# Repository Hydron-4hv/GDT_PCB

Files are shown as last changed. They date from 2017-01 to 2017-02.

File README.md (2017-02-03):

# GDT_PCB
PCB for drive circuitry and Gate Drive Transfomer, for driving IGBT half-bridge PCBAs in Tesla Coil application

# WARNING:
The creepage/clearance distances on this PCB between the bridge voltages (i.e. those present of the output of the GDT) and the low voltage circuitry is not large (1mm), and thus nothing connected to this PCB (including the driver controller connected via the RJ45 connectors) should be touched while mains voltage is applied. Unless an isolation tranformer is used to supply the bridge DC bus voltage, everything except mains protective earth should be treated as live.

Notes:
- To be used with the PCB from the either the "IGBT_half_bridge" or "QCW_half_bridge_PCB" repos, 2 off for full bridge setup, 4 for dual full-bridge.
- A hand wound gate drive transformer is required.
  - I am planning to wind one with RG-174 co-ax (for high coupling), with primary side being the shield, secondary being the centre conductor.
  - A full bridge setup needs 2 windings on each core, and won't use all four winding connections or output connectors.
  - Will supply pictures once I have built the PCB and wound the transformers
- To drive extra half bridges a second PCB can be "slaved" to the first using the expansion connection. An output variant has been created named "SLAVE" to show this
- PDF schematics, 3D info, BoMs etc are located within the "Reference Outputs" directory
- Note that the regulator for the "12V" net is actually a 5V output part - anything in the range of 5V-12V should work OK.
- The 24V input can be lowered if the desired gate drive voltage to the IGBTs is less than this.
- The 3x 1000uF 25V capacitors are unnecessarily large for low pulse length applications (e.g. standard non-QCW DRSSTC). These should be replaced by smaller, 35V rated parts if the board is not used in a CW or QCW application.

Note: changes planned for next revision:
- Improve creepage distance as possible. Isolation slots.
- Potential to add transformer isolation for CT input from ribbon cables
- Use RS485 for gate drive signal input from RJ45 for increased noise immunity. (High priority)
- Add power status LED
- "12V" to be renamed to "5V", and supply also used for RS485 receiver
- Use switchmode DC/DC on the PCB rather than in a module
- Capacitor voltage specifications in "Gate Driver" sub section to be increased to 35/50V from 25V. Parts are available in the same package with increased rating.
- Fix DC jack footprint (add locating hole)
- Potential addition of fan/temperature control/measurement
- Change TVS footprints for fitting lower capacitance parts (e.g. SOT-23)
- Fix major pinout problem for drive FETs (CAD software decided to flip component for no reason)

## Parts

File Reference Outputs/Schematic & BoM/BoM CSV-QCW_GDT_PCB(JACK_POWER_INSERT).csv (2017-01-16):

Designator | Comment | Description | Fitted | Footprint | LibRef | Quantity
A_1, A_2, B_1, B_2 | Testpoint |  | Fitted | Keystone5002 | Testpoint | 4
C1, C2, C3 | EEU-FM1E102 | CAP ALUM 1000UF 20% 25V RADIAL | Fitted | 12.5mm lytic | Electrolytic Capacitor | 3
C4, C5, C31_1, C31_2 | CC0805KKX7R7BB105 | CAP CER 1UF 16V X7R 0805 | Fitted | 0805C | Capacitor | 4
C6, C7 | 885012209028 |  | Fitted | 1210C | Capacitor | 2
C26_1, C26_2 | GRM31MR71H105KA88L | CAP CER 1UF 50V X7R 1206 | Fitted | 1206C | Capacitor | 2
C27_1, C27_2, C30_1, C30_2 | 885012209028 | CAP CER 10UF 25V X7R 1210 | Fitted | 1210C | Capacitor | 4
C28_1, C28_2 | CGA6M3X7R1H225K200AB | CAP ALUM 100UF 20% 16V RADIAL | Fitted | 1210C | Capacitor | 2
C29_1, C29_2, C32_1, C32_2 | 08055C104JAT2A | CAP CER 0.1UF 50V X7R 0805 | Fitted | 0805C | Capacitor | 4
C37_1, C37_2, C38_1, C38_2 | C0805C102K5RACTU | CAP CER 1000PF 50V X7R 0805 | Fitted | 0805C | Capacitor | 4
D1, D2 | 600 W, 24 VDC | WE-TVSP Power TVS Diode, bidirectional, 600 W, 24 VDC | Fitted | DO-214AA_Bidirectional | WE-TVSP DO-214AA, 824521241 | 2
D7_1, D7_2, D8_1, D8_2 | MCL4148-TR | DIODE GEN 75V 150MA MICROMELF | Fitted | MicroMELF | 1N4148 | 4
FB1, FB2, FB3, FB4 | FerriteBead | Ferrite Bead | Fitted | 0805FB | FerriteBead | 4
J1, J3, J5, J7 | 61202021621 | WR-BHD 2.54mm Male Box Header | Fitted | 61202021621 | 61202021621 | 4
J2, J4 | 61500814221 | WR-MJ Modular Jack Horizontal Shielded 8P8C Tab Down | Fitted | 61500814221 | 61500814221 | 2
J6 | BNC_1 | BNC Connector | Fitted | BNC_PLASTIC_ELBOW_SOCKET_WITH_MOUNTING_POSTS | BNC_1 | 1
J8, J13 | 22-23-2021 | Pin Header, 2 Position, Locking, .1 Centers | Fitted | 22-23-2021 | 22-23-2021 | 2
J9 | 61201621621 | WR-BHD 2.54mm Male Box Header | Fitted | 61201621621 | 61201621621 | 1
J10 | POWER_J | Low Voltage Power Supply Connector | Fitted | POWER_J_SLOT |  | 1
J11 | Header_3_right_angle_th_3.81mm | 3-way header | Fitted | 691322310003 | Header_3_right_angle_th_3.81mm | 1
J12 | Header_2_5.08mm_Screw_Black | 2-way PCB connector | Not Fitted | 1776119-2 | Header_2_5.08mm_Screw_Black | 0
Q3_1, Q3_2, Q4_1, Q4_2 | DMC3021LK4-13 | MOSFET N/P-CH 30V TO252-4L | Fitted | TO-252 | FDD8424H | 4
R1 | 30R 1W |  | Fitted | RES_2512 | Resistor | 1
R2, R3 | 10R 1W |  | Fitted | RES_2512 | Resistor | 2
R4, R5, R6, R7, R33_1, R33_2, R37_1, R37_2 | RC0805FR-071KL | RES SMD 1K OHM 1% 1/8W 0805 | Fitted | 0805R | Resistor | 8
R8 | 0R |  | Not Fitted | 1206R | Resistor | 0
R9 | 0R |  | Fitted | 1206R | Resistor | 1
R34_1, R34_2 | CRCW121015R0JNEAHP | RES SMD 15 OHM 5% 3/4W 1210 | Fitted | 1210R | Resistor | 2
TX1, TX2 | DIY_GDT | DIY Gate Drive TX on 36x22x14 toroid | Fitted | GDT_DIY | GDT_DIY | 2
TX3, TX4, TX5 | 80uH | WE-CST Current Sense Transformer, EE5, 80uH | Fitted | WE-CST_EE5 | WE-CST, 749251020 | 3
U1, U2 | USB6B1 | USB Data Line Protection | Fitted | SOIC-8 | USB6B1 | 2
U3 | FDSM, 173010578 | MagI³C-FDSM Fixed Step Down Regulator Module | Fitted | WE-FDSM_173010x78 | FDSM, 173010578 | 1
U5_1, U5_2 | MIC4126YME | IC DRIVER MOSFET 1.5A DUAL 8SOIC | Fitted | SOIC-8 | UCC27423D | 2

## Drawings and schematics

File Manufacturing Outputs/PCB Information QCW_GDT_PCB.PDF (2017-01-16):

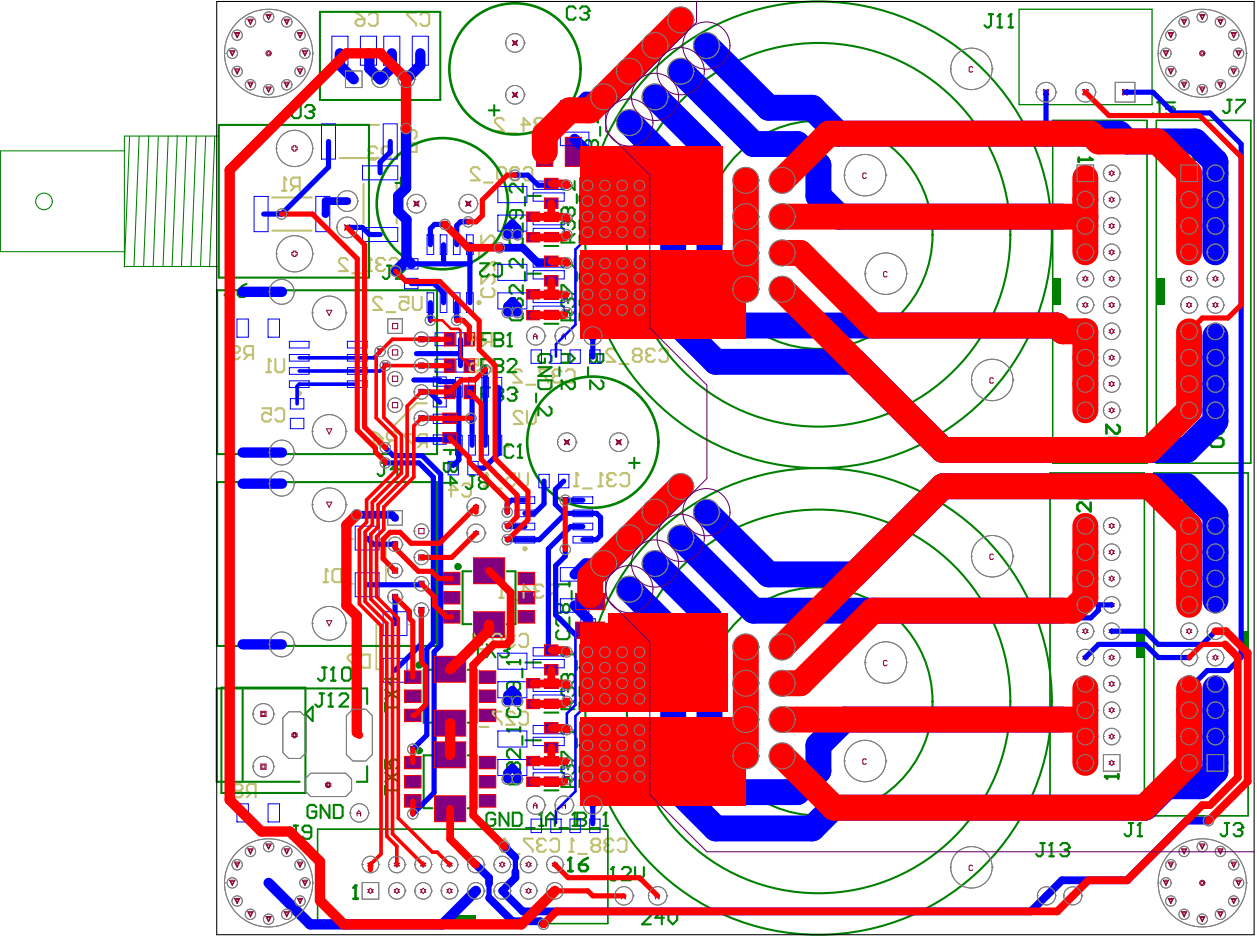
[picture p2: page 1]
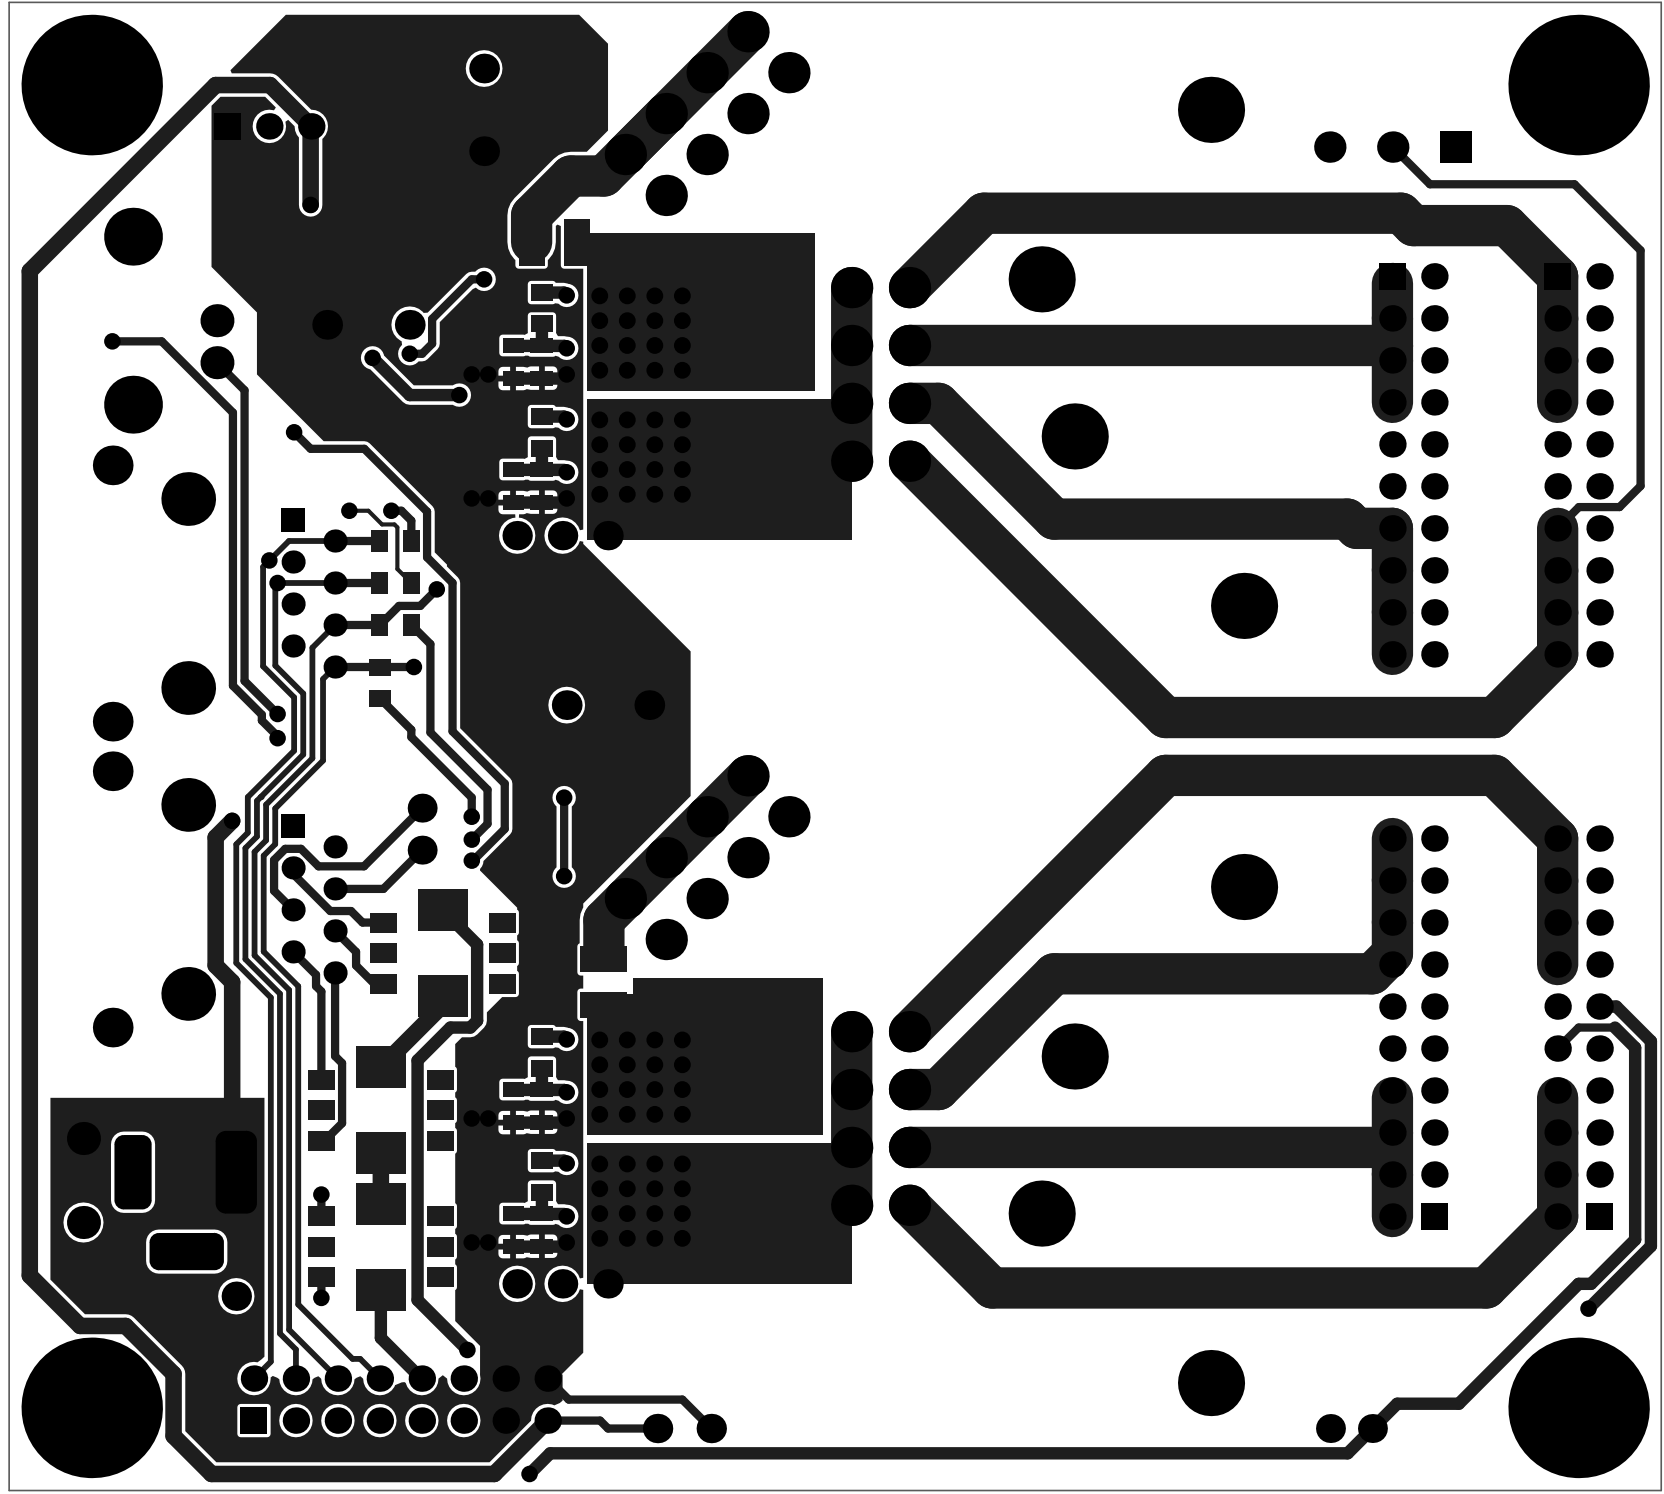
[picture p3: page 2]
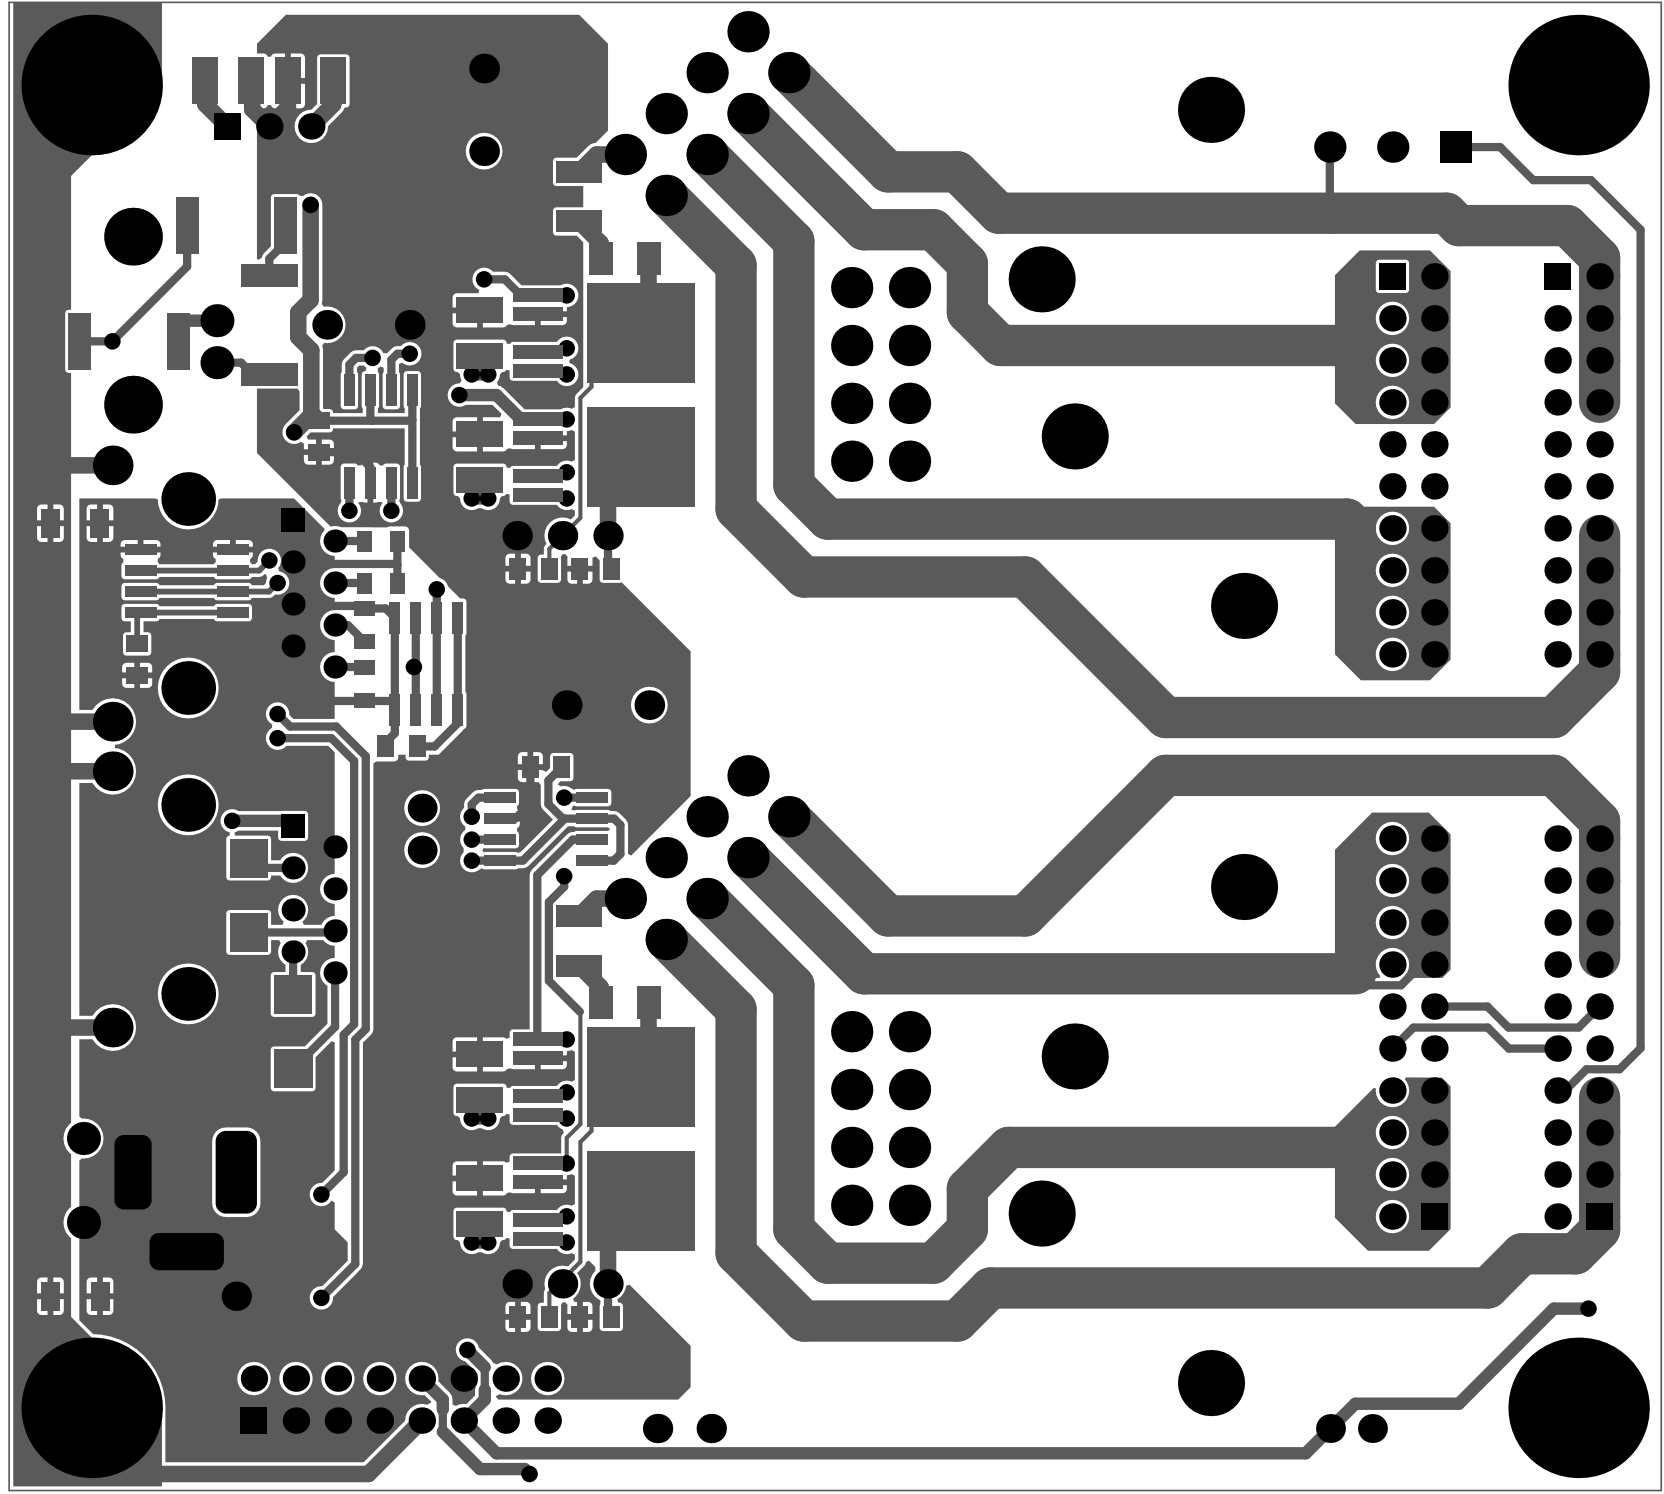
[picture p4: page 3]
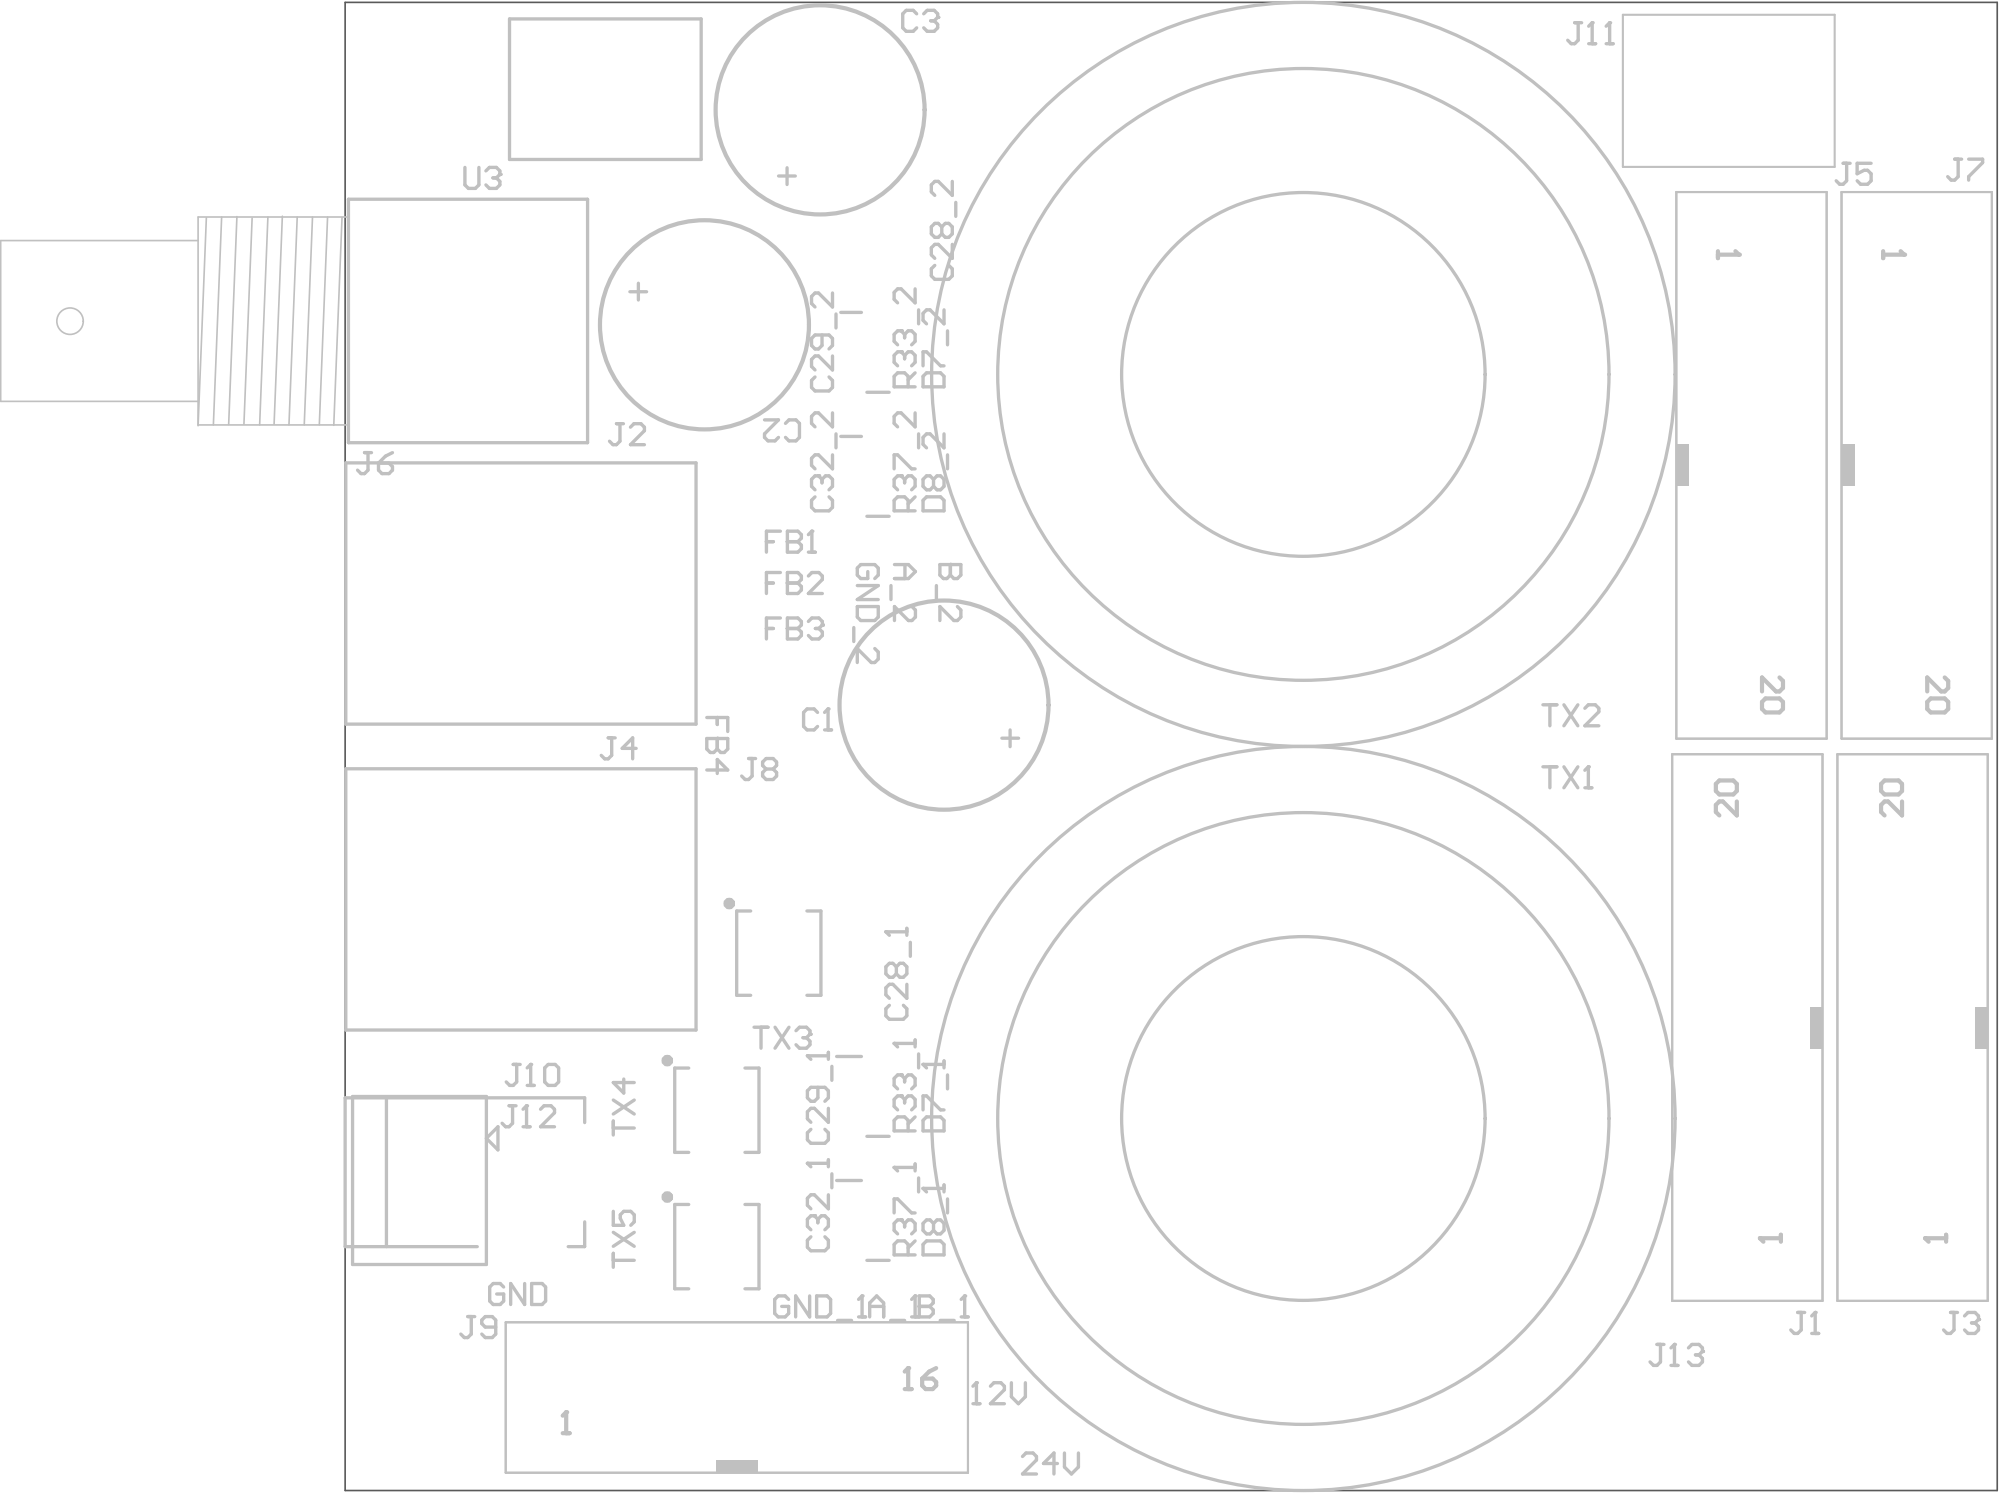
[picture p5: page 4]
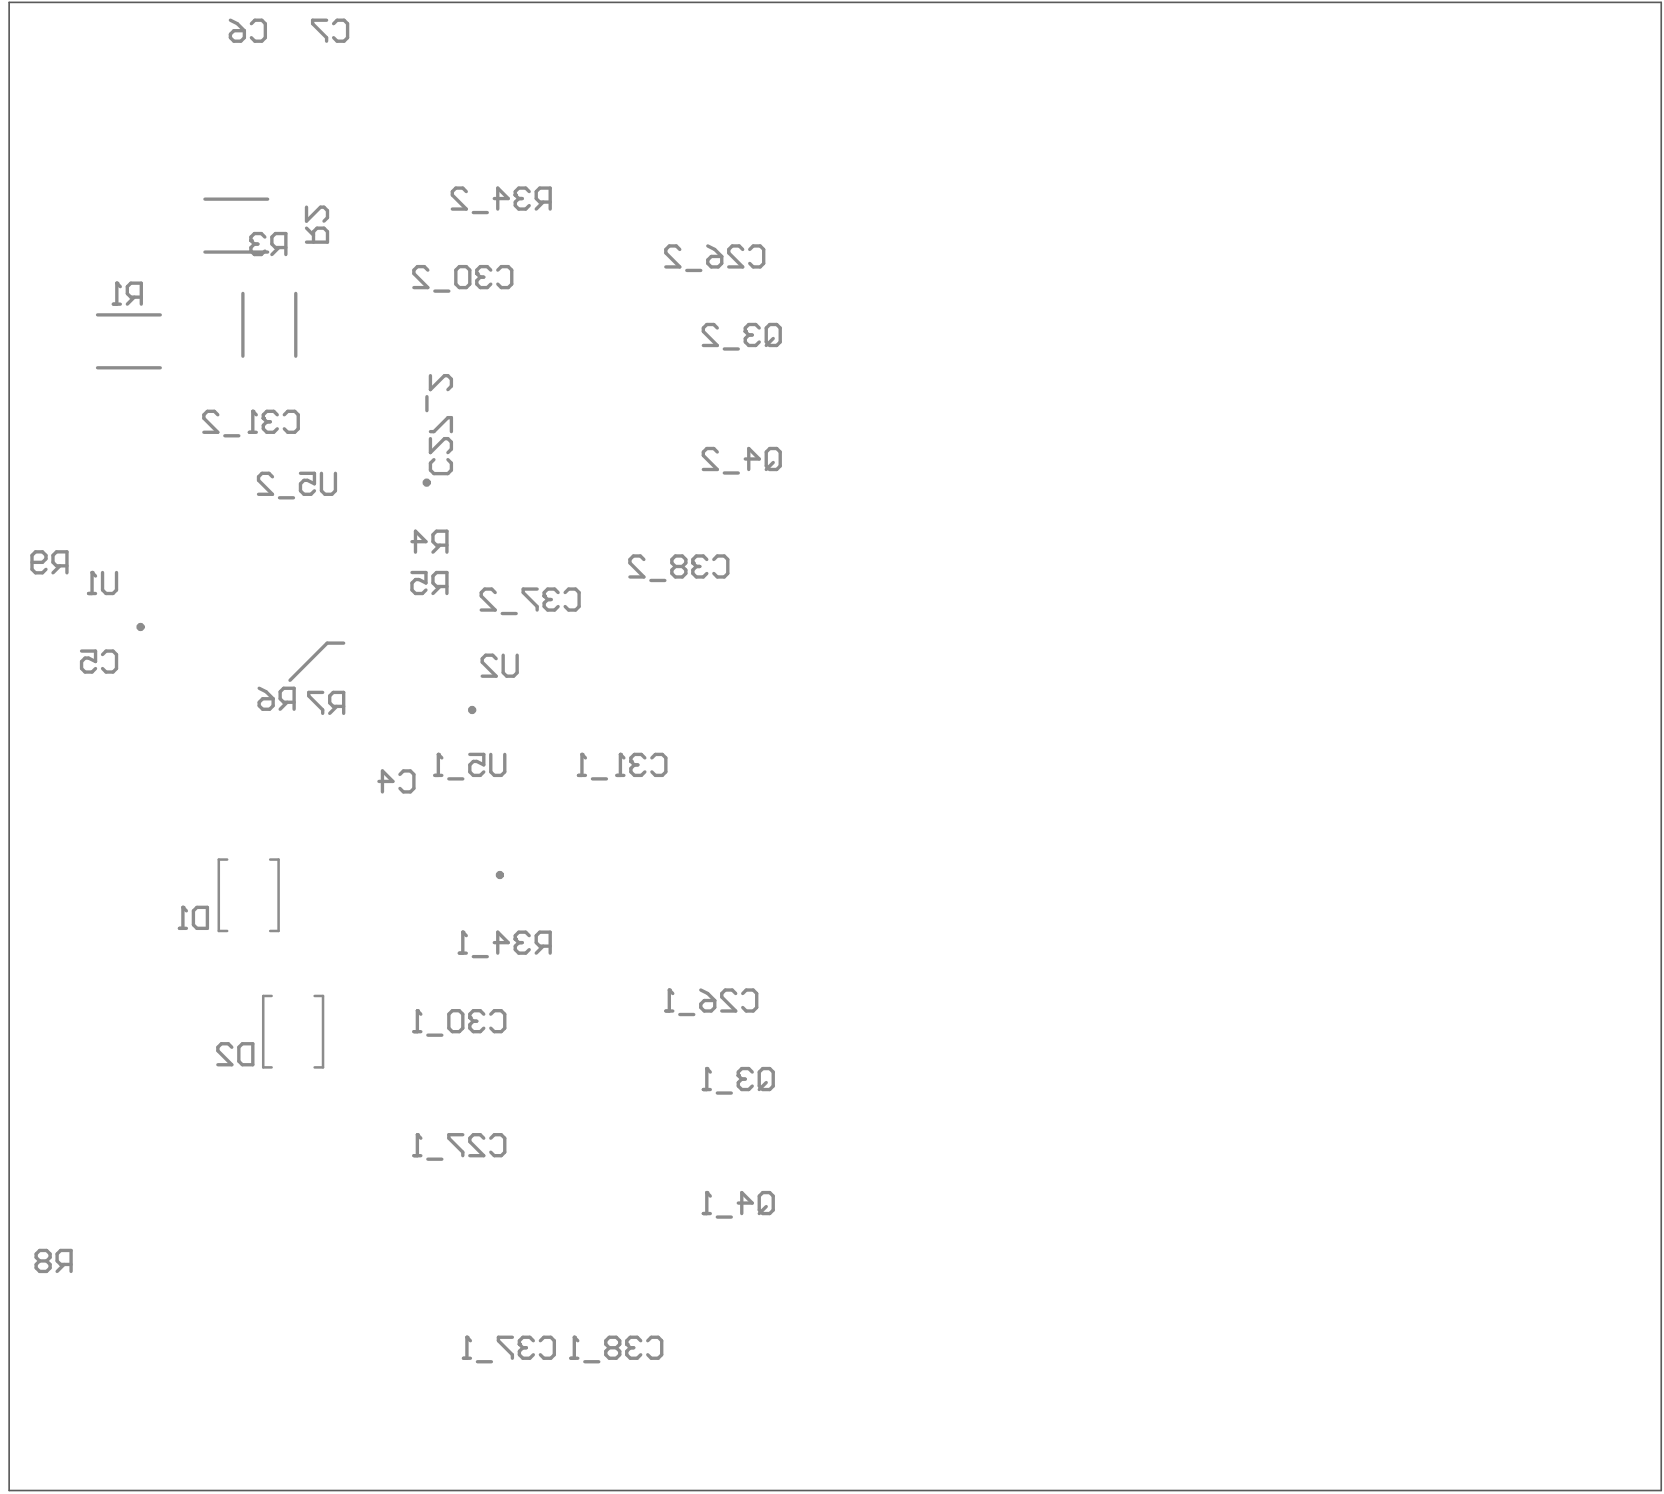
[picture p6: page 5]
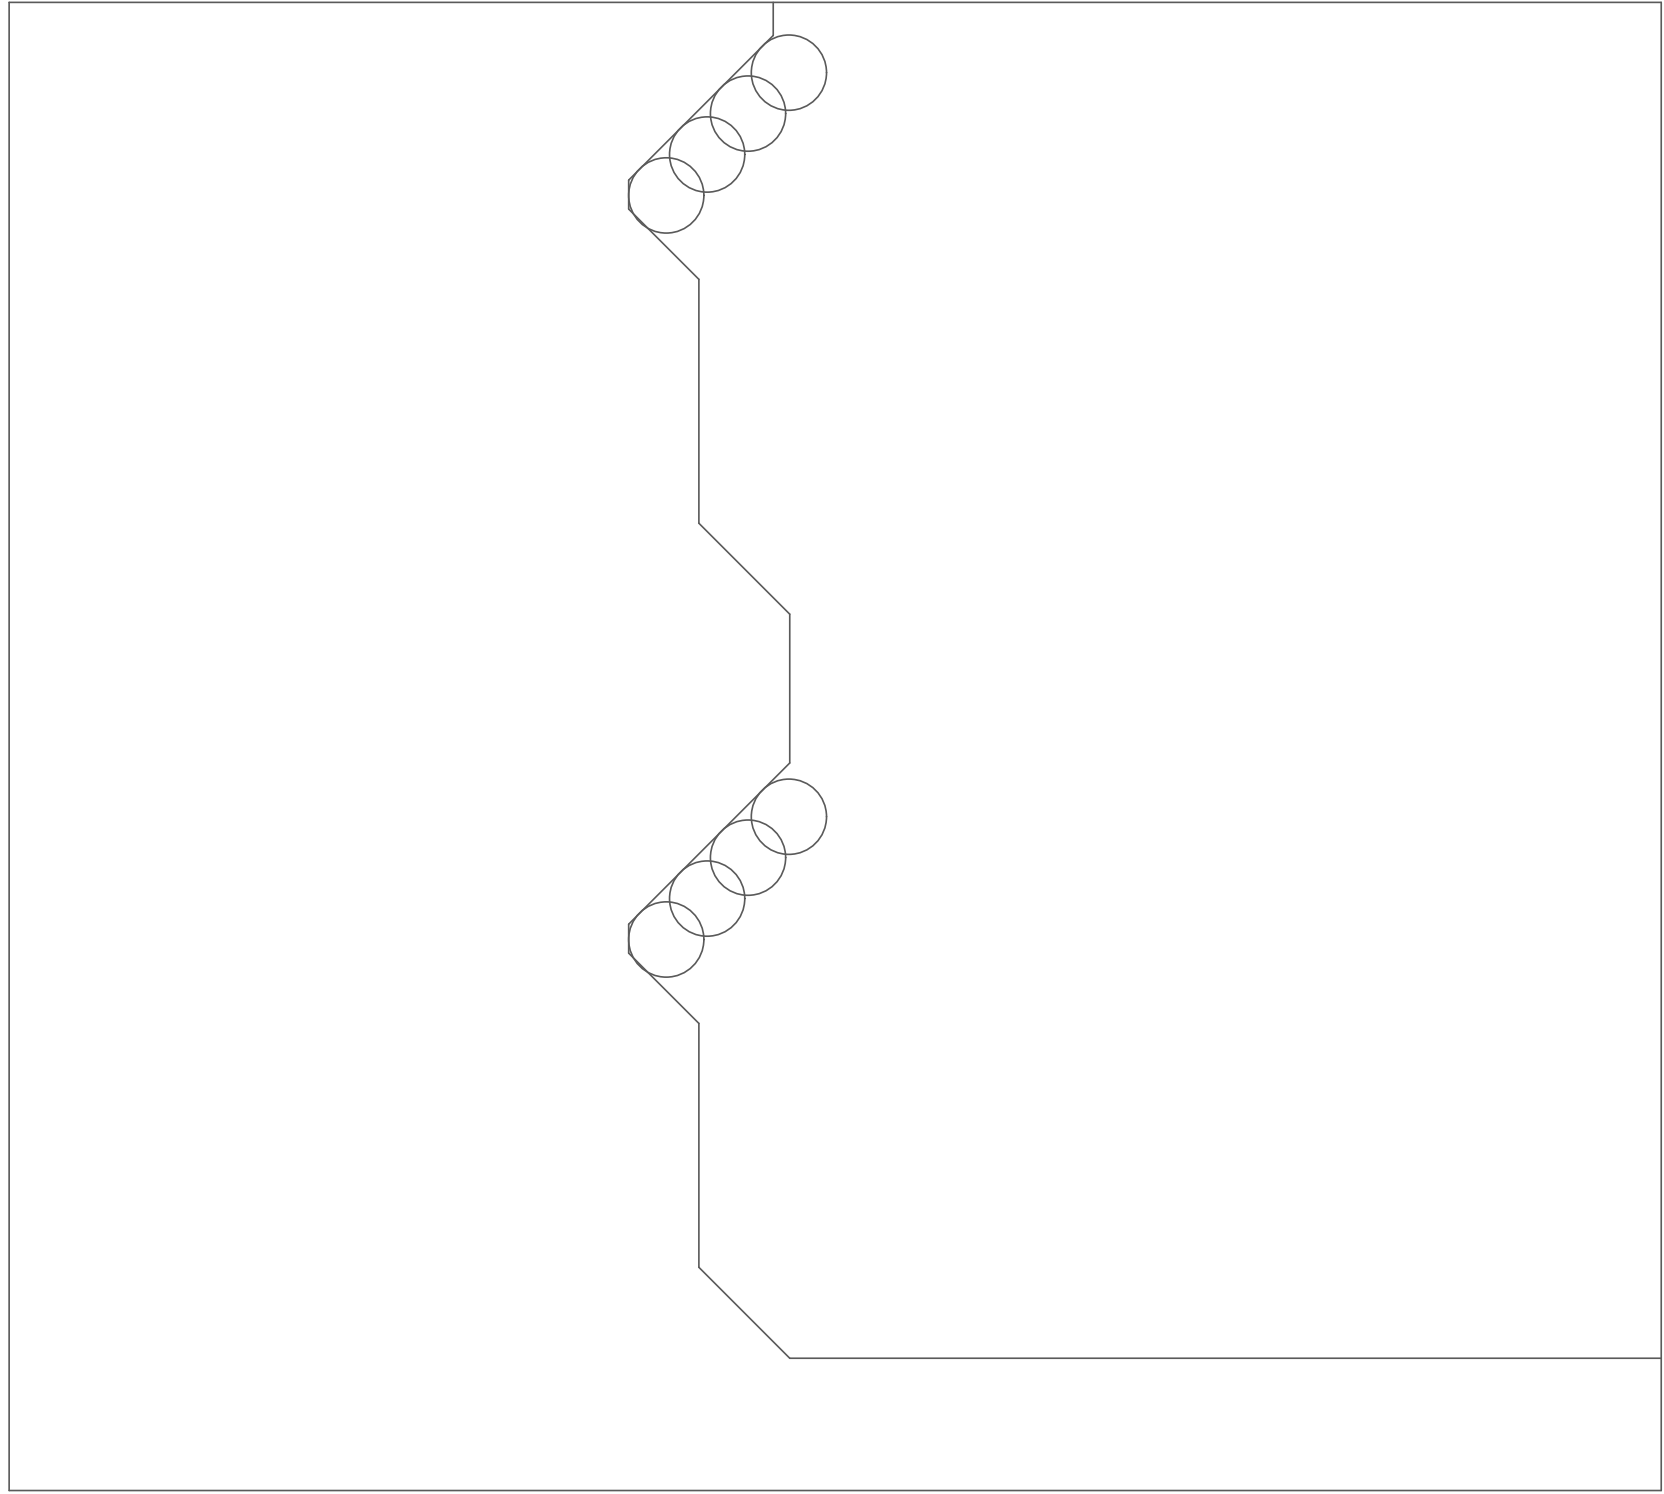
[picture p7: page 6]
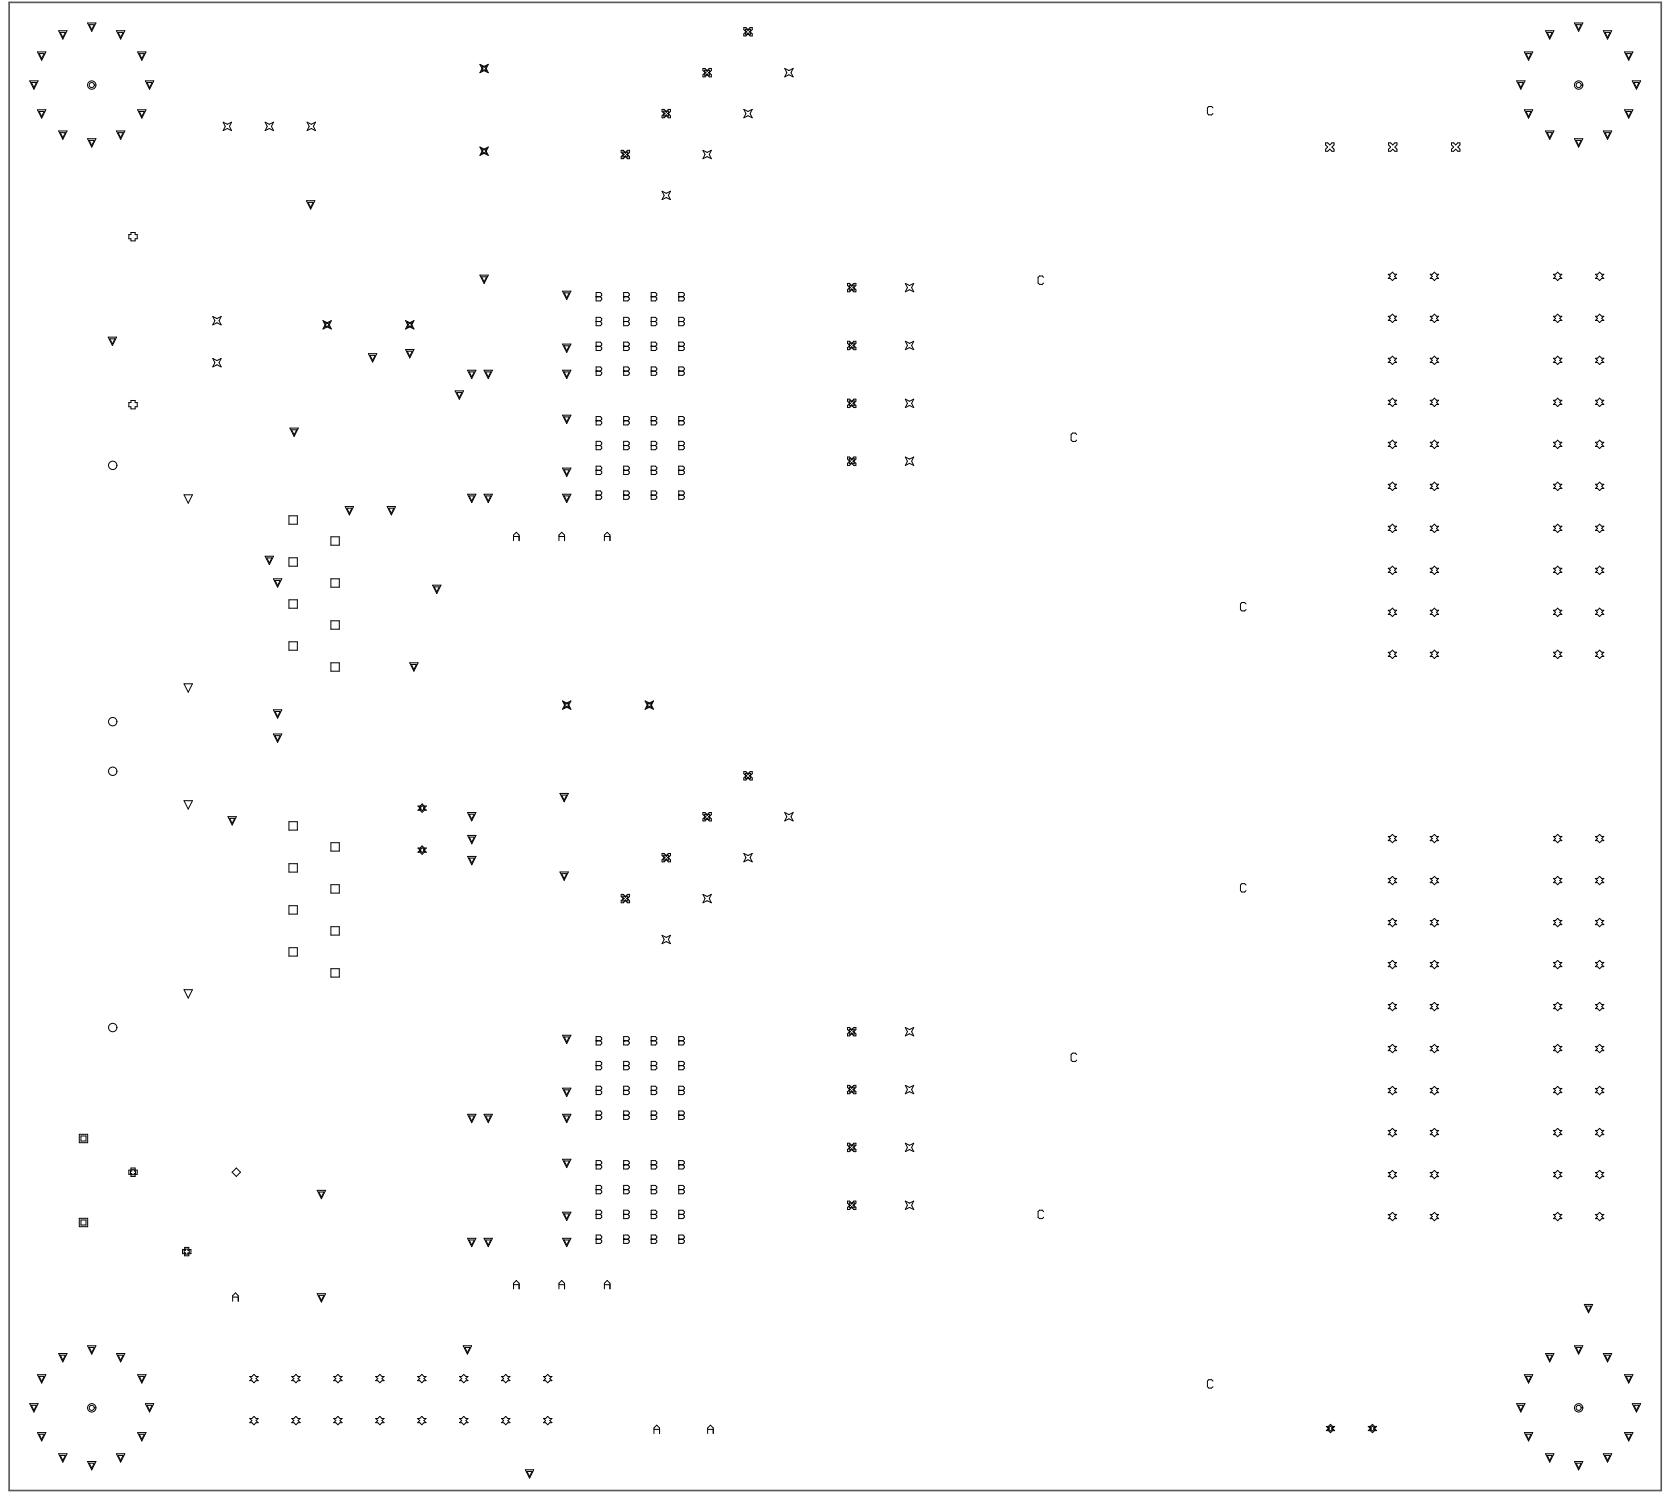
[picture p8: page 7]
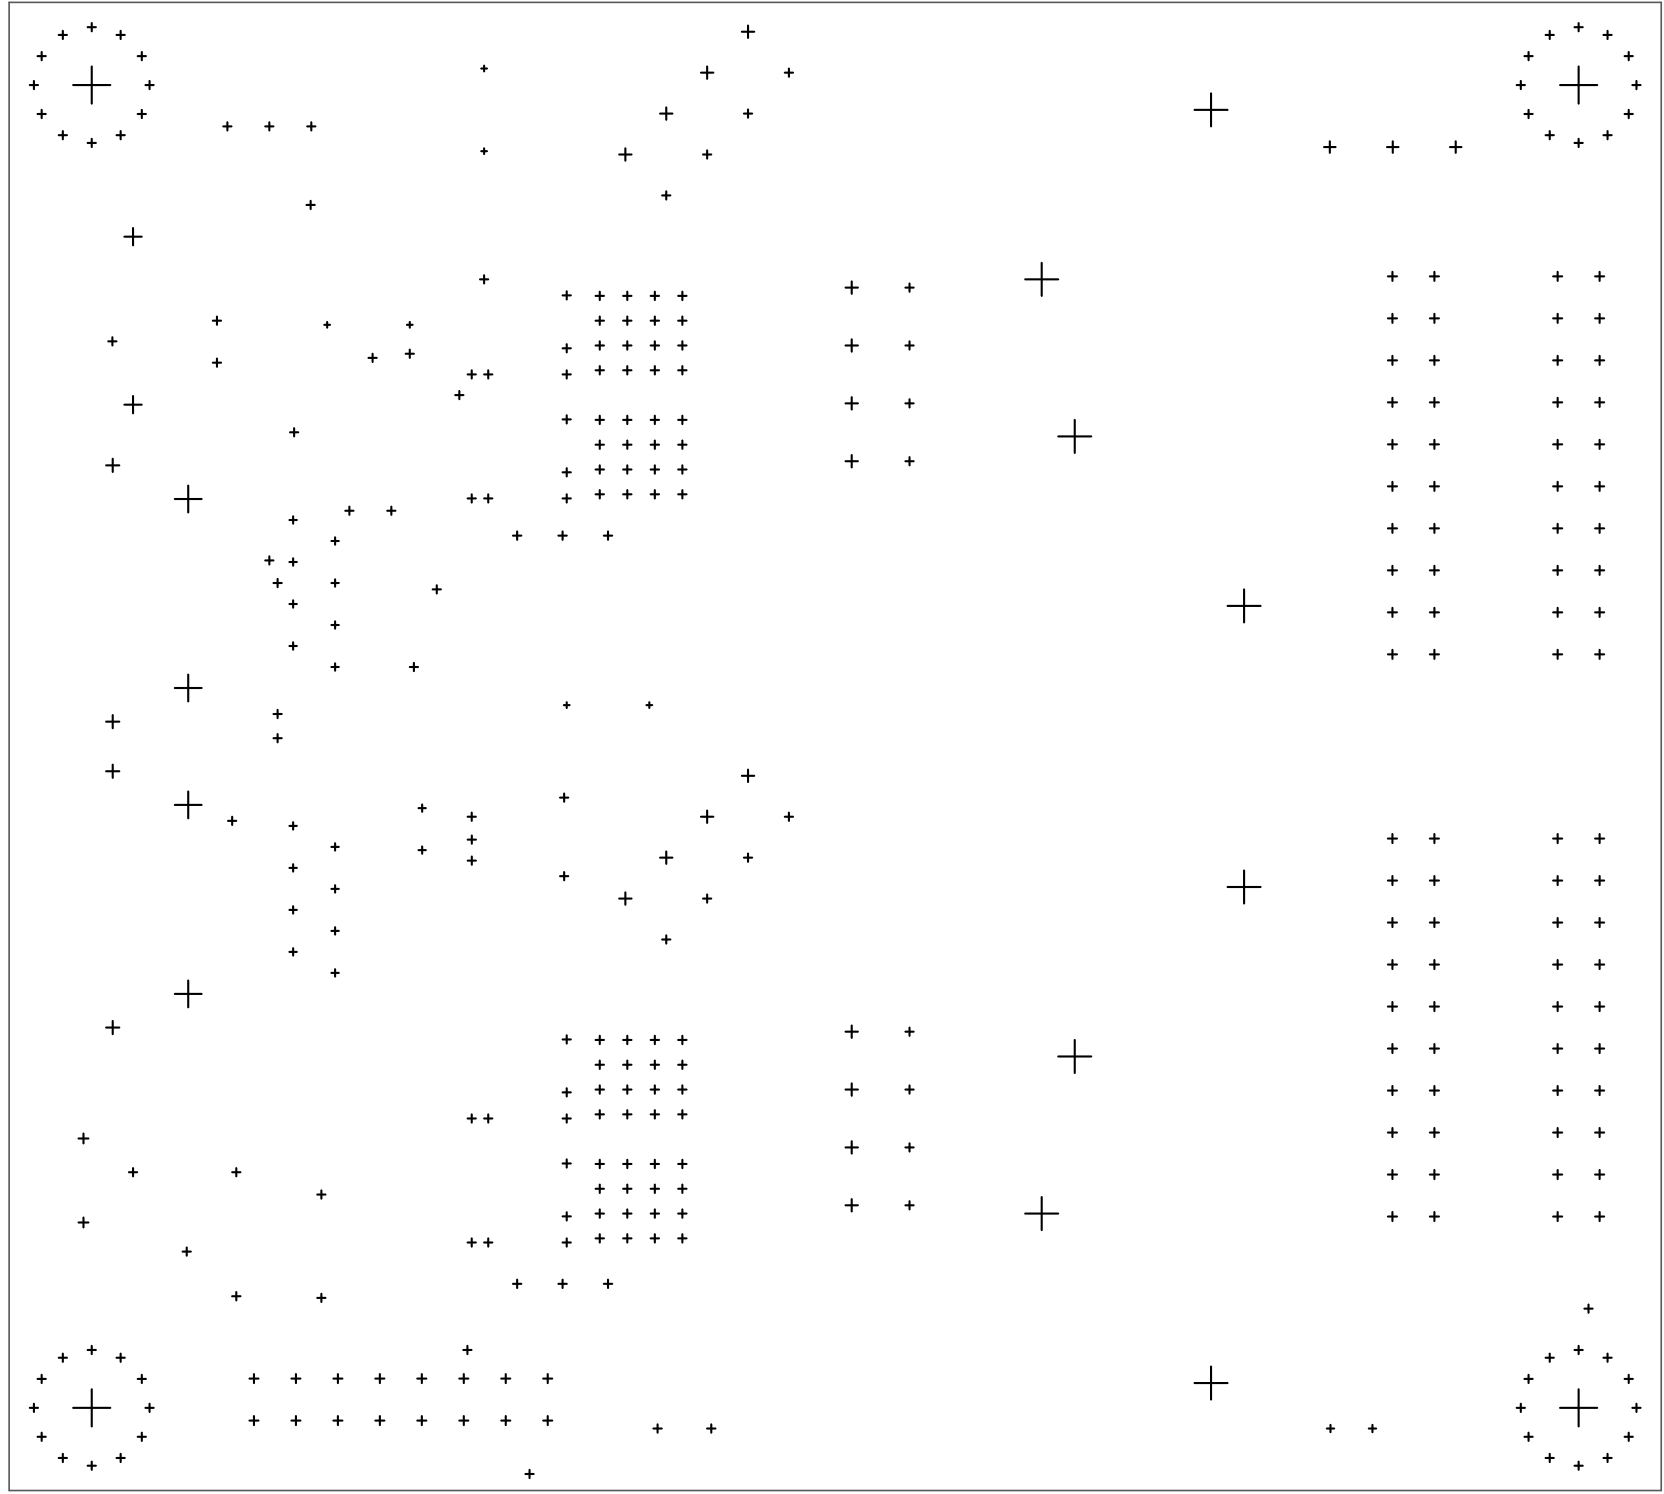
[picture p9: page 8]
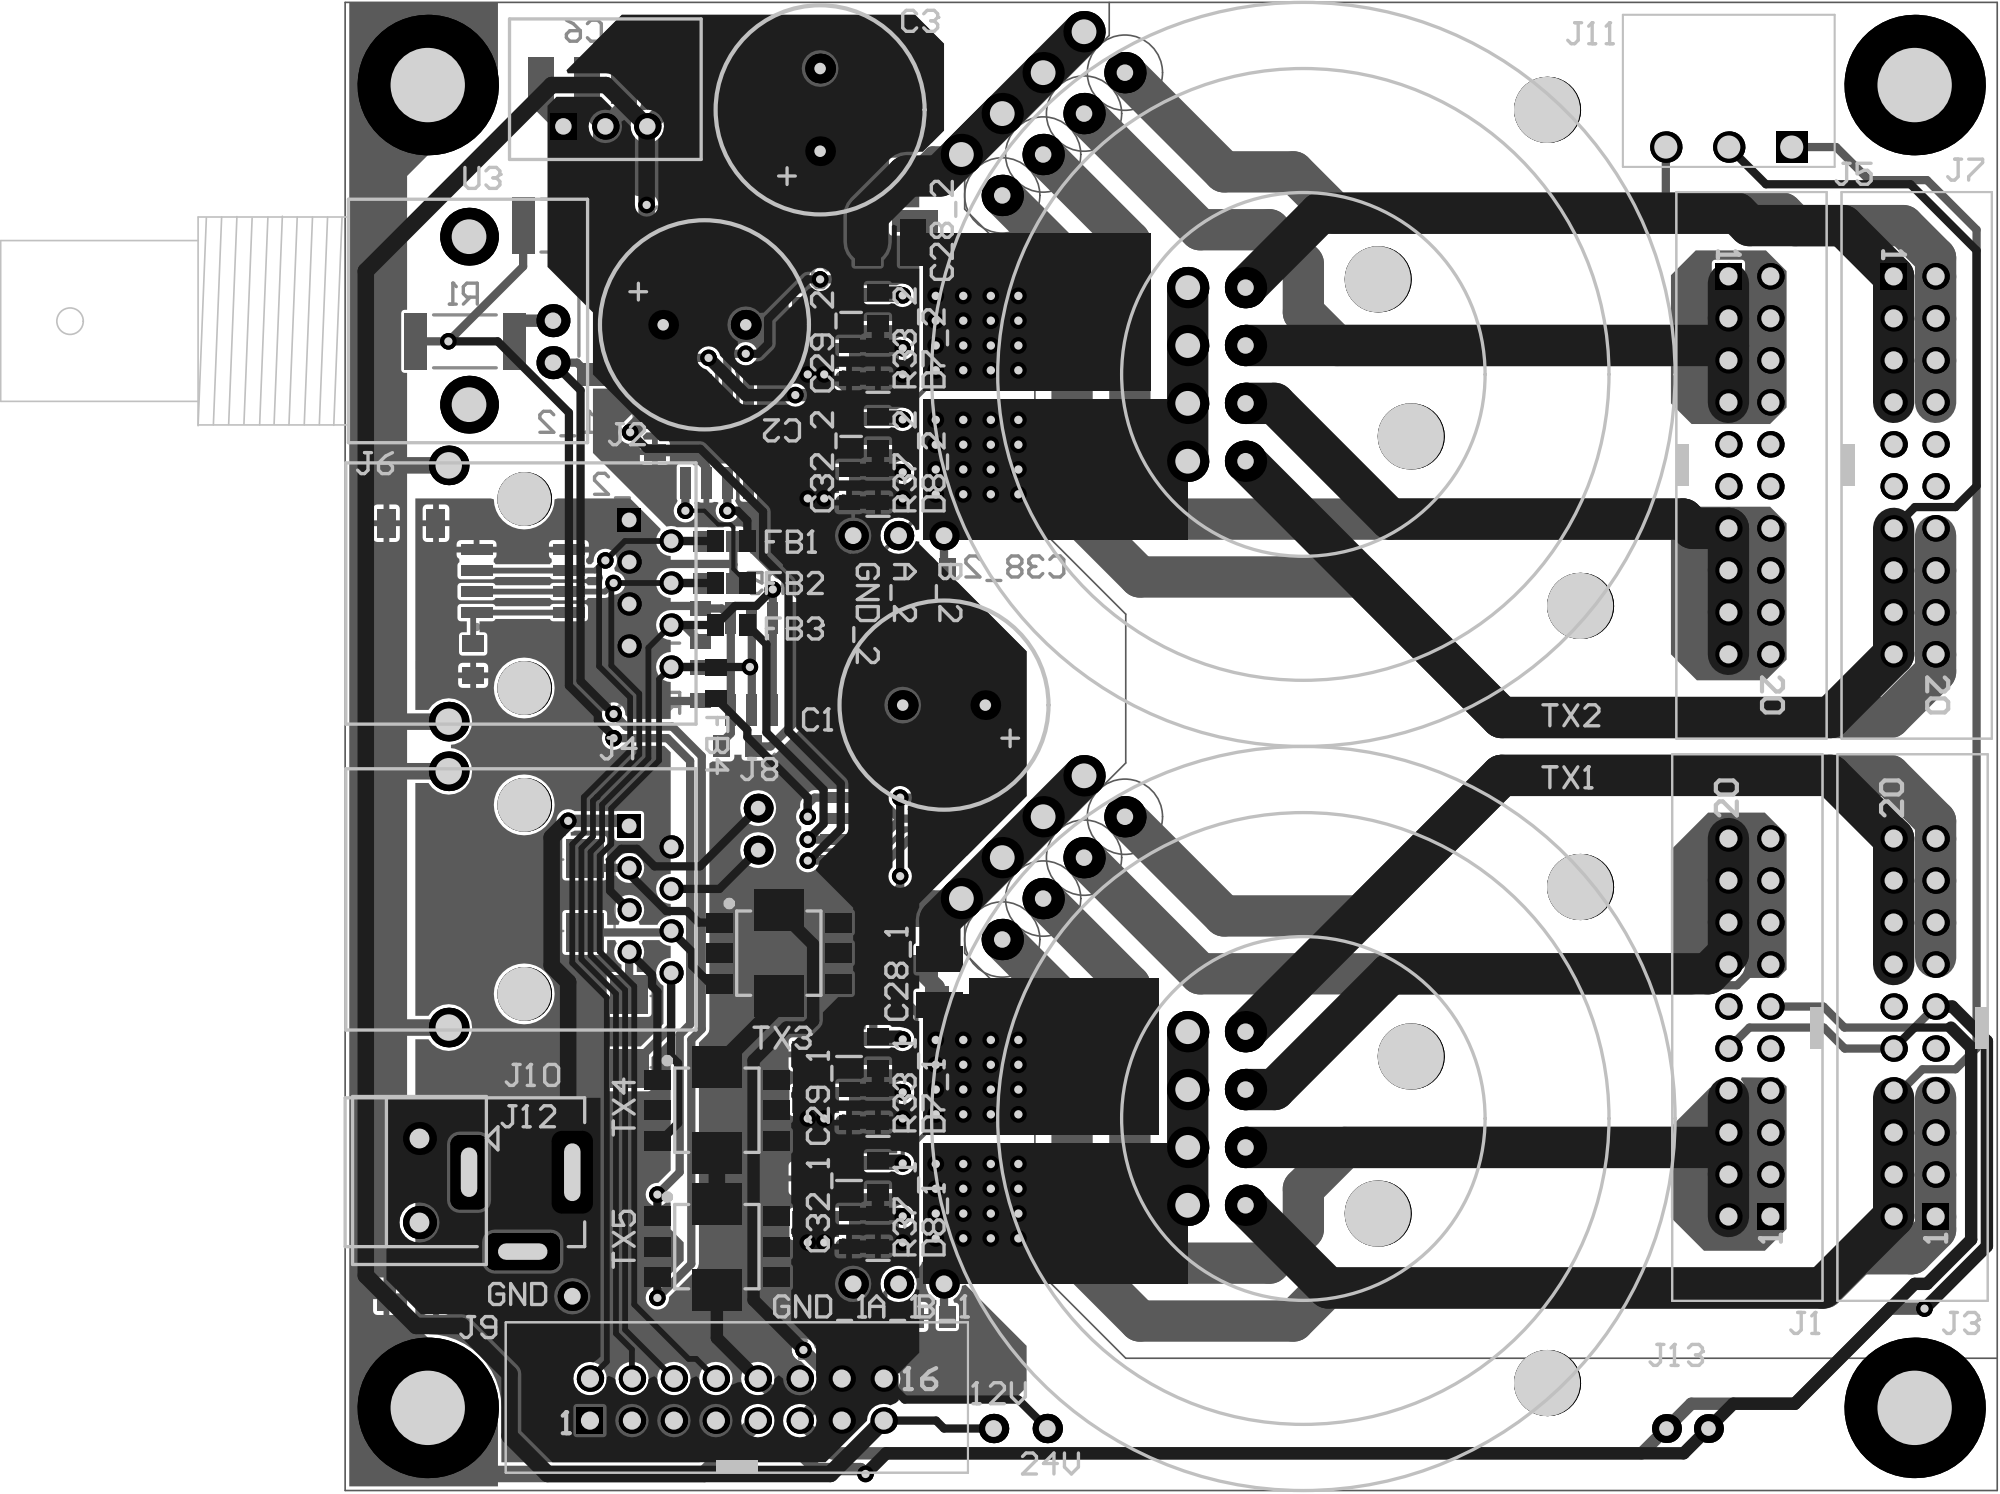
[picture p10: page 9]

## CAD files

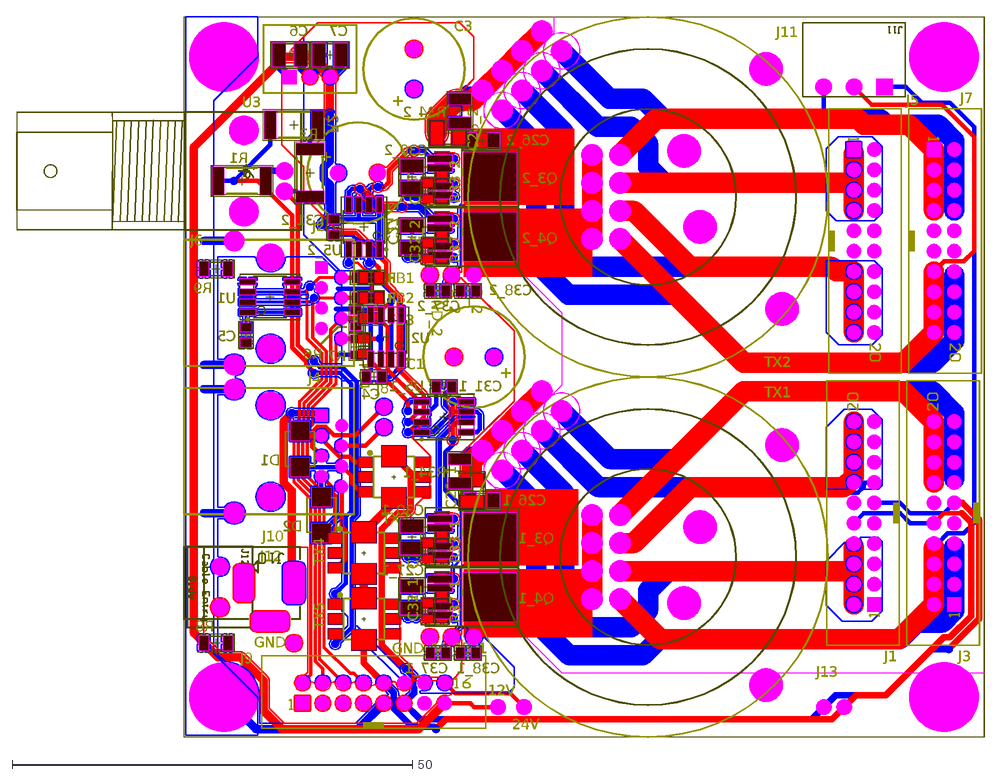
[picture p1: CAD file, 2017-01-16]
Reference Outputs/Mechanical/QCW_GDT_PCB.DXF
R7
R6
R5
R4
GND
GND_2
GND_1
24V
J12
C3
C2
C1
J8
J9
D2
D1
J1
J2
J3
J4
J5
J6
J7
R1
R2
R3
TX3
TX4
TX5
J11
J10
A_1
A_2
B_1
B_2
C26_1
C26_2
C27_1
C27_2
C28_1
C28_2
C29_1
C29_2
C30_1
C30_2
C31_1
C31_2
C32_1
C32_2
C37_1
C37_2
C38_1
C38_2
D7_1
D7_2
D8_1
D8_2
FB1
FB2
FB3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
